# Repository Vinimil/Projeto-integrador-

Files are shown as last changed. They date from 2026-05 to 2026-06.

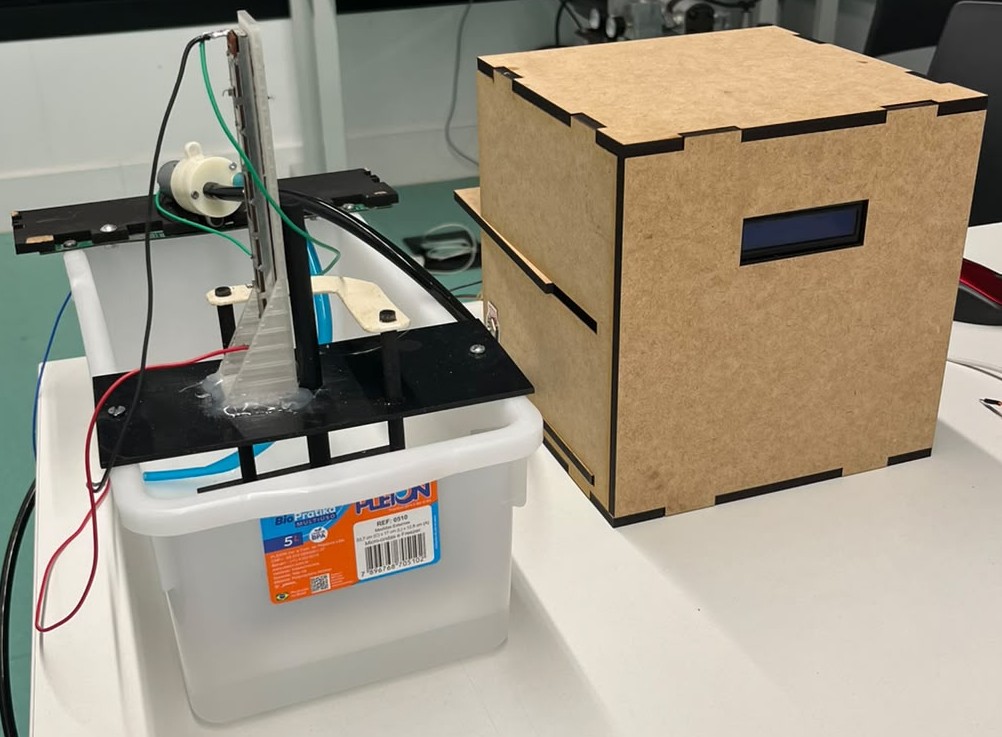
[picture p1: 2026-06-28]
Imagem projeto2.jpg

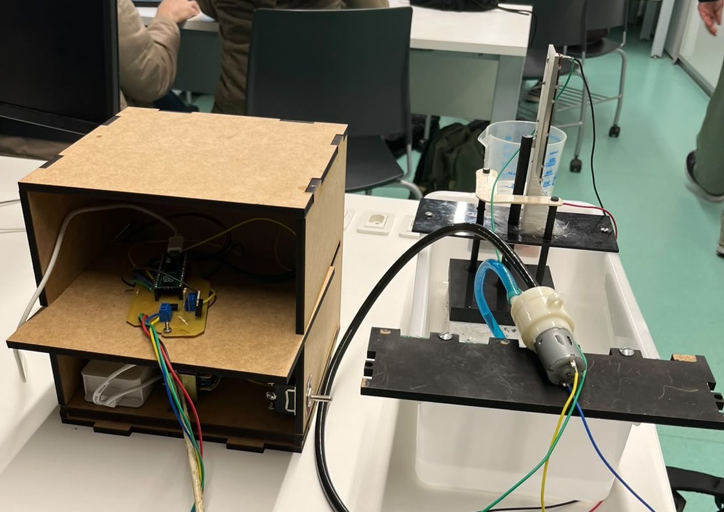
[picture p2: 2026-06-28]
Imagem projeto1.jpg

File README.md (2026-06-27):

Sistema de Dosagem Automática de Água com Raspberry Pi Pico

1.Integrantes:

João Lourenço Medeiros Martins (RA: 22.00369-0)
Nicolas Lemos Nunes Tamashiro (RA: 22.00728-8)
Theo Franchin Peres (RA: 22.01094-7)
Vinicius Filgueiras dos Santos (RA: 23.95007-2)

2.Descrição do projeto:

Este projeto propõe um sistema embarcado de automação para controle de nível e dosagem volumétrica de fluidos entre reservatórios (TK-101 e TK-102), utilizando um Raspberry Pi Pico (RP2040) como unidade central de processamento. A automação integra um transdutor de nível resistivo (potenciômetro linear) condicionado por filtros digitais FIR, IHM em display LCD I2C e acionamento de potência via optoacoplamento e MOSFET, garantindo isolamento galvânico e controle preciso de vazão por modulação de pulsos.

3.Objetivos:

-Realizar dosagem precisa retirando líquido de um reservatório principal.
-Converter a posição do sensor em volume real (mL).
-Permitir a seleção de dosagens pré-definidas.
-Controlar automaticamente a bomba hidráulica.
-Interromper a dosagem ao atingir o volume desejado.
-Exibir informações do processo em um display LCD.
-Implementar estratégia de controle em malha fechada via realimentação.

4.Arquitetura do Sistema:

4.1 Composição:
-Reservatório 1: Principal (medição e retirada).
-Reservatório 2: Receptor.
-Sensor de Nível: Potenciômetro linear acoplado a flutuador.
-Raspberry Pi Pico: Responsável por aquisição de sinais, conversão ADC, processamento, controle da bomba e interface LCD.
-Módulo MOSFET: Acionamento da bomba.
-Display LCD 16x2 I2C: Interface visual.

4.2 Funcionamento Geral:
-Leitura do sensor de nível.
-Conversão ADC (12 bits) para valor digital.
-Conversão do valor ADC para volume (mL) via tabela de calibração.
-Seleção de dosagem pelo usuário.
-Cálculo do erro de dosagem em tempo real e acionamento da bomba via malha fechada com realimentação contínua, utilizando zonas de tempo (1200ms, 700ms e 300ms) para amortecimento da inércia mecânica.
-Leitura, verificação do volume transferido e correção, repetindo o ciclo até atingir a meta.

5.Hardware:

Componente             Conexão

Potenciômetro          Terminal 1: 3V3 / Cursor: GP26 (ADC0) / Terminal 2: GND
Display LCD	           VCC: 5V / GND: GND / SDA: GP8 / SCL: GP9
MOSFET	Gate           GP15
Terminal 1	           3V3
Cursor	               GP26 (ADC0)
Terminal 2	           GND
A bomba  é alimentada externamente 

Display:

LCD 16x2
Interface I2C
Endereço: 0x27

5.1 Características:

Alimentação: 3,3 V
Saída analógica
Ligado diretamente ao ADC do Pico

6.Estratégia de Medição e Calibração:

-Conversão ADC: Escala de 0 a 4095.
-Filtragem: Média de 500 amostras consecutivas seguida por um filtro de 20 leituras úteis.
-Calibração: Utilização de tabela experimental com interpolação linear para valores intermediários.
-Pontos de calibração: 
ADC	Volume (mL)
3057	0
3054	200
3041	400
529	3000

7.Estratégia de Controle

-Malha Fechada: Realimentação baseada no volume calculado.
-Controle por Pulsos:
-Região Longa: Pulsos de 1200 ms (alta velocidade).
-Região Intermediária: Pulsos de 700 ms (redução de velocidade).
-Região Final: Pulsos de 300 ms (ajuste fino para precisão).
-Correção de Volume:
-Fator de 1.22 para dosagens de 250 mL.
-Fator de 1.44 para dosagens de 300 mL e 350 mL.

8.Interface LCD e Resultados:

Status de Operação: Tela inicial, Dosagem em execução e Processo finalizado.
Resultados Observados: O sistema apresentou repetibilidade satisfatória, com resultados médios de ≈ 250 mL, ≈ 300 mL e ≈ 350 mL para as respectivas doses solicitadas.

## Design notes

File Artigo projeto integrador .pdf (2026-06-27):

SISTEMA EMBARCADO PARA CONTROLE E MEDIÇÃO VOLUMÉTRICA DE

RESERVATÓRIOS: UMA ABORDAGEM DE BAIXO CUSTO UTILIZANDO O

MICROCONTROLADOR RP2040

João Lourenço Medeiros Martins¹; Nicolas Lemos Nunes Tamashiro¹; Theo Franchin

Peres¹; Vinicius Filgueiras dos Santos¹; Andressa Corrente Martins²; Rodrigo de Marca

França²

¹ Docente do Instituto Mauá de Tecnologia (IMT)

² Docente do Instituto Mauá de Tecnologia (IMT)

Resumo

Este artigo apresenta o desenvolvimento, a implementação e a validação

experimental de um sistema embarcado de automação concebido para o

monitoramento contínuo e o controle em malha fechada da transferência volumétrica de

fluidos entre reservatórios. A arquitetura de hardware baseia-se no microcontrolador

RP2040, explorando seu conversor analógico-digital de 12 bits para a aquisição de

dados provenientes de um transdutor de nível resistivo, construído por meio do

acoplamento mecânico de um potenciômetro linear a um flutuador fixado em uma

estrutura manufaturada em PLA. Com o intuito de mitigar as perturbações

hidrodinâmicas e outras interferências, o sinal analógico foi condicionado por um filtro

passa-baixas passivo e processado por um filtro digital FIR de médias móveis. A

estratégia de controle atua por realimentação contínua, compensando os efeitos da

inércia do atuador (bomba de diafragma de corrente contínua) por meio de um

algoritmo de comutação dividido em três faixas de erro. A calibração da leitura foi

realizada mediante interpolação linear por partes e a aplicação de fatores corretivos

(1,22 e 1,44). Os ensaios comprovaram a resiliência da malha, registrando erro relativo

máximo de -2,40% e erro relativo nulo dentro da resolução experimental para a meta de

300 mL. O protótipo atesta a viabilidade do emprego de instrumentação alternativa para

processos de pequena escala.

Palavras-chave: RP2040. Realimentação Contínua. Instrumentação Eletrônica.

Automação. Filtro Digital.

### 1 INTRODUÇÃO

### 1 INTRODUÇÃO

No contexto da automação de processos industriais e laboratoriais, a exatidão no

controle e na dosagem contínua de fluidos é um requisito importante para garantir a

qualidade e a repetibilidade operacional (Bolton, 2015). A expansão dos sistemas

embarcados voltados à automação tem impulsionado o desenvolvimento de soluções

de baixo custo e alta confiabilidade, oferecendo uma alternativa técnica e

economicamente viável aos sensores industriais tradicionais (Dorf; Bishop, 2011).

Este trabalho apresenta o desenvolvimento, a implementação e a validação

experimental de um sistema automatizado para monitoramento e controle volumétrico

da transferência de água entre dois reservatórios. A planta didática, projetada conforme

a norma ISA 5.1 (ISA, 2024), é composta pelos tanques TK-101 e TK-102, interligados

hidraulicamente, sendo a variável controlada o volume de água transferido entre eles.

O processamento dos sinais do transdutor de nível e o acionamento dos

elementos finais de controle são realizados pelo microcontrolador RP2040 (Raspberry

Pi Foundation, 2024). O sistema realiza a conversão analógico-digital das leituras do

sensor, executa uma malha fechada de controle e disponibiliza as informações ao

operador por meio de uma Interface Homem-Máquina (IHM) baseada em display LCD

16×2 com comunicação I2C, além da transmissão de dados via porta serial (UART).

Devido à inércia da bomba de diafragma, à latência do escoamento e às

limitações de resolução do sensor, foi desenvolvida uma estratégia de controle baseada

em filtragem digital, calibração empírica e acionamento do atuador por comutação em

faixas de erro, visando aumentar a precisão da dosagem e a estabilidade do sistema.

### 2 MATERIAIS E MÉTODOS

A metodologia adotada foi dividida em três etapas interrelacionadas: o

desenvolvimento do arranjo mecânico, a implementação do hardware eletrônico de

condicionamento, e a implementação da malha de realimentação no firmware.

### 2.1 Estrutura Mecânica e Transdutor Analógico

A aferição contínua do nível baseia-se em um transdutor resistivo baseado em

um potenciômetro linear acoplado. O cursor metálico de um potenciômetro deslizante

foi fixado mecanicamente a uma haste sólida tracionada por um flutuador no

reservatório TK-101. Para assegurar a ortogonalidade do movimento e prevenir o

travamento provocado por esforços laterais, desenvolveu-se uma estrutura de suporte

mecânico rígida. O esquemático de interligação dos reservatórios e do sistema de

bombeamento pode ser visualizado na Figura 1, detalhando a topologia adotada.

Figura 1 - Esquemático do sistema detalhando a interligação entre os tanques e a

bomba.

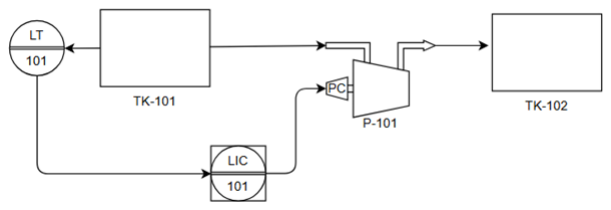
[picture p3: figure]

Fonte: Elaborado pelos autores (2026).

As peças e as fixações do potenciômetro foram modeladas em ambiente CAD

tridimensional utilizando o software SolidWorks e manufaturadas em uma impressora

3D com polímero ácido polilático (PLA), conforme ilustra a Figura 2, que evidencia o

arranjo físico projetado para a haste.

Figura 2 - Modelagem em CAD (SolidWorks) das fixações estruturais do transdutor.

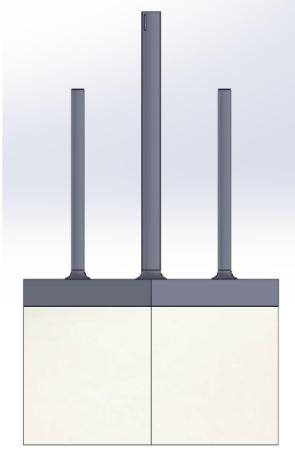
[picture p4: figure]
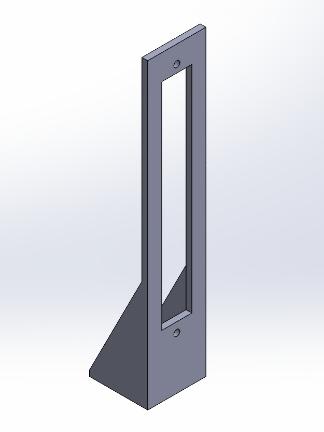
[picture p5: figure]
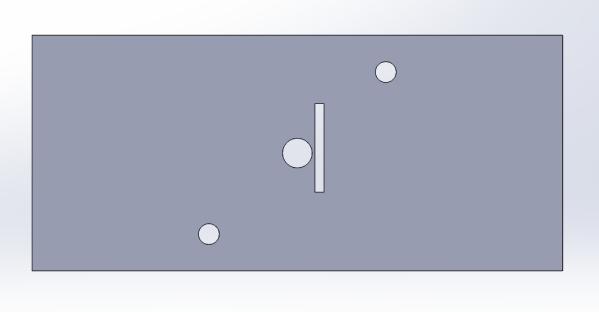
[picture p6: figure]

Fonte: Elaborado pelos autores (2026).

O divisor de tensão resultante no cursor do potenciômetro é polarizado por uma

tensão de referência restrita de 3,3 V, de modo que o deslocamento físico da boia

acompanhando o nível do fluido se traduz proporcionalmente em variação de potencial

elétrico encaminhada ao canal de conversão (ADC) do microcontrolador.

### 2.2 Microcontrolador e Condicionamento de Sinais

O processamento centraliza-se no microcontrolador RP2040. A fim de atenuar os

ruídos e as interferências acopladas aos condutores do sensor resistivo, foi projetado

um filtro analógico passa-baixas passivo composto por uma rede resistor-capacitor

(RC).

Adotando-se um componente resistivo de 10 kΩ e uma capacitância de 100 nF, a

frequência de corte (fc) teórica, segundo as premissas de Sedra e Smith (2014), é

calculada pela Equação 1:

fc =

1
2π. R. C

=

1
2π. 10. 10³. 100. 10⁻⁹ = 159,15 Hz

Este limiar de aproximadamente 159 Hz reduz os fenômenos de aliasing elétrico

de alta frequência, mantendo as componentes de baixa frequência originadas da

movimentação mecânica.

### 2.3 Circuito de Potência e Isolamento Galvânico

Devido às limitações de capacidade de corrente das portas GPIO do microcontrolador e

à imperatividade de proteção contra transientes indutivos, foi implementado um estágio

de acionamento baseado em comutação por estado sólido.

A interface entre o subsistema de controle (3,3V) e o estágio de potência (7,5V) é

realizada mediante isolamento galvânico via optoacoplador PC817. Esta topologia

assegura a segregação elétrica completa, mitigando o acoplamento de ruídos e

transientes de tensão induzidos pela carga indutiva das bombas ao microcontrolador.

Em conformidade com as diretrizes de integridade de sinal, a topologia da PCB contempla a separação estrita entre os planos de terra (GND) dos domínios de controle

e de potência.

O sinal de controle, após atravessar o isolador, é aplicado ao terminal de gate de um

transistor MOSFET, configurado para operar como chave de estado sólido. A transição

para nível lógico alto satura o optoacoplador, polarizando o gate e conduzindo o

MOSFET à região de condução, permitindo o acionamento da carga via Low-Side

Switching. Esta configuração possibilita a comutação eficiente de cargas de 10A,

garantindo estabilidade térmica e a integridade da lógica de controle. Adicionalmente, a

robustez operacional do sistema é assegurada pela utilização de fontes de alimentação

independentes: um barramento de 5V dedicado à unidade de processamento (RP2040)

e display, e um barramento isolado de 7,5V exclusivo para o estágio de potência das

bombas permitindo a topologia de isolamento.

Figura 3 – Diagrama Elétrico

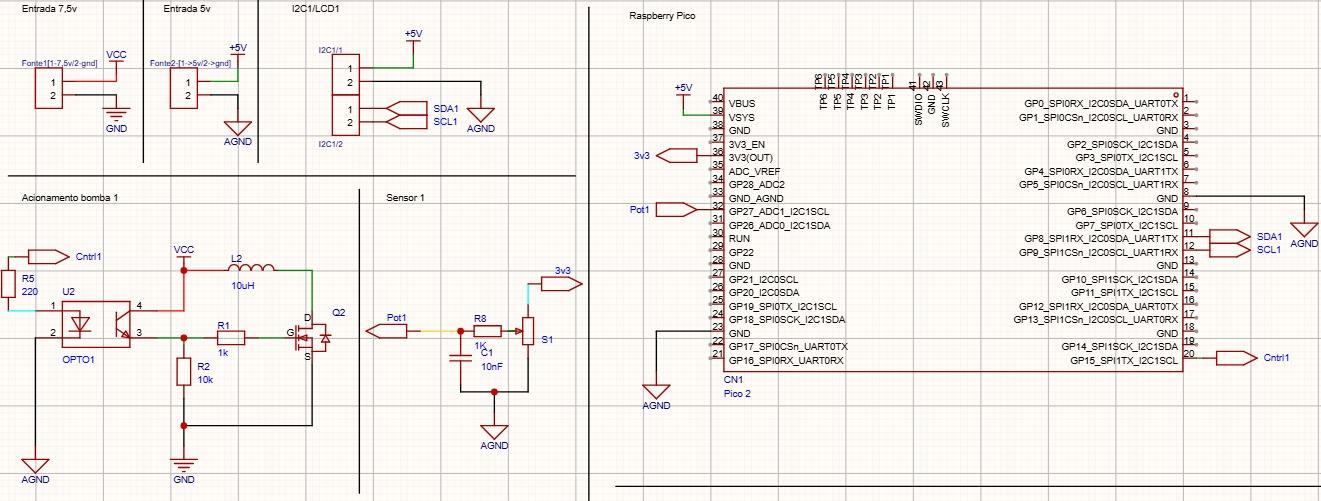
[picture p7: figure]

Fonte: Elaborado pelos autores (2026).

### 2.4 Modelagem Algorítmica e Filtragem Digital

O sinal digitalizado no ADC (0 a 4095) encontra-se sujeito a oscilações da

superfície do líquido durante o impacto do recálque. Implementou-se no firmware um

filtro digital Finite Impulse Response (FIR) por médias móveis. O algoritmo consolida a captura contínua de 500 amostras analógicas consecutivas por ciclo. Em seguida, essa

saída alimenta uma segunda janela de filtragem restrita que retém as últimas 20

leituras, garantindo a atenuação significativa dos ruídos transientes.

Devido ao atrito mecânico, o sistema apresenta falhas de linearidade nas pontas

da escala. Parametrizou-se em software uma tabela relacionando pontos específicos de

leitura a volumes hídricos reais (calibração). Para estimar em tempo real os volumes

situados entre os pontos de calibração, o sistema executa uma interpolação linear

paramétrica segmentada, descrita pela Equação 2:

V = V1 + [

ADC − ADC1
ADC2 − ADC1

]. (V2 − V1)

Onde V é o volume de fluido estimado em tempo real; ADC é a leitura

instantânea filtrada do conversor; ADC1 e ADC2 são os limites tabelados vizinhos à

leitura; e V1 e V2 denotam os volumes absolutos correspondentes a esses limites.

### 2.5 Estratégia de Controle e Realimentação Contínua

A topologia adotada atua através de uma malha fechada direta de realimentação

contínua. O diagrama de blocos apresentado na Figura 4 apresenta essa arquitetura: o

sinal captado pelo sensor de nível é injetado em um nó comparador interno no RP2040,

gerando continuamente o sinal de erro em relação à meta arbitrada. Com base neste

erro, o microcontrolador processa a resposta e atua sobre a bomba de diafragma, cujo

fluxo físico altera o nível do reservatório e realimenta o laço do sensor.

Figura 4 - Diagrama de blocos do sistema, evidenciando o laço de realimentação

contínua de estado.

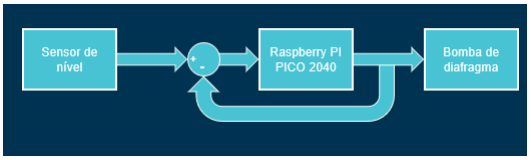
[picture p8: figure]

Fonte: Elaborado pelos autores (2026).

Para reduzir o escoamento residual da tubulação (fluido remanescente em

escoamento após a remoção da alimentação elétrica), o atuador não opera de maneira

simples (Liga/Desliga direto), sendo modulado em três zonas de tempo baseadas na

amplitude instantânea do erro:

- Região de Erro Elevado (Erro > 180 mL): Acionamento da bomba em janelas

largas de 1200 ms.

- Região de Erro Intermediário (50 mL < Erro ≤ 180 mL): Redução do tempo de

pulso para 700 ms, induzindo gradiente de desaceleração.

- Região de Erro Crítico (Erro ≤ 50 mL): Saturação ativa com pulsos de 300 ms,

para correção de ajuste fino.

Inseriu-se um tempo morto (dead time) compulsório de 300 ms após cada ciclo

de pulso, permitindo que a ondulação do fluido se estabilize antes de uma nova leitura

ser consolidada no comparador. O ganho estático foi parametrizado em 1,22 para

dosagens de 250 mL e 1,44 para as metas superiores.

O comissionamento e o monitoramento operacional são estabelecidos por meio

de um módulo de cristal líquido (LCD 16x2) com expansor I2C. A interface foi

programada para fornecer ao operador um feedback visual dinâmico em tempo real: a

primeira linha do display apresenta a variável analógica bruta processada pelo ADC,

denominada T (referente à tensão normalizada do potenciômetro), enquanto a segunda

linha exibe o Volume atual calculado após a aplicação das rotinas de filtragem FIR e da

interpolação linear parametrizada. Essa estrutura de exibição garante a supervisão

direta da conversão eletroeletrônica do sinal, permitindo a validação visual imediata da

calibração do sensor.

### 3 RESULTADOS E DISCUSSÃO

A certificação da integridade da planta experimental baseou-se na execução de

ensaios repetitivos e parametrizados. Extraiu-se um conjunto de ensaios onde os

volumes transferidos ao TK-102 foram quantificados mediante um copo graduado,

validando a eficácia e a repetibilidade da lógica proposta visando as metas volumétricas

de 250 mL, 300 mL e 350 mL.

A Tabela 1 expõe a consolidação da capacidade corretiva dos fatores

matemáticos adotados na modelagem, refletindo o desvio numérico após a aplicação

do laço de realimentação.

Tabela 1 - Desempenho metrológico e erro relativo das dosagens automatizadas.

Meta definida (mL) | Leitura Bruta do Sensor (mL) | Volume Estimado Corrigido (mL) | Aferição Real Medida (mL) | Erro Relativo (%)
250 | 173 | 249 | 244 | -2,40
300 | 209 | 301 | 300 | 0,00
350 | 243 | 350 | 348 | -0,57

Fonte: Elaborado pelos autores (2026).

A análise sistemática aponta para um desempenho satisfatório. Nas

aproximações nominais de 300 mL e 350 mL, as margens relativas demonstraram alta

concordância (registrando 0,00% e -0,57%, respectivamente). Na região de dosagem

reduzida (250 mL), o erro relativo permaneceu no teto administrável de -2,40%.

Ensaios preliminares sem a modulação por zonas resultavam em sobre-dosagem

maciça (overshoot) variando entre 15% e 20% acima do setpoint. O motor continuava

rotacionando devido ao momentum da bomba de diafragma, e a coluna residual

pendente drenava gravitacionalmente. A fragmentação do esforço de controle nas

janelas de 1200, 700 e 300 milissegundos reduziu essa extrapolação.

Para elucidar a eficácia da regressão linear, os gráficos a seguir ilustram as

curvas de calibração empírica relacionando o volume real retirado com a estimativa

processada. Observa-se a correção da histerese e a convergência após a aplicação

dos fatores multiplicativos correspondentes (1,22 e 1,44).

Gráfico 1 - Curva de calibração comparativa para a meta de 250 mL (Fator 1,22).

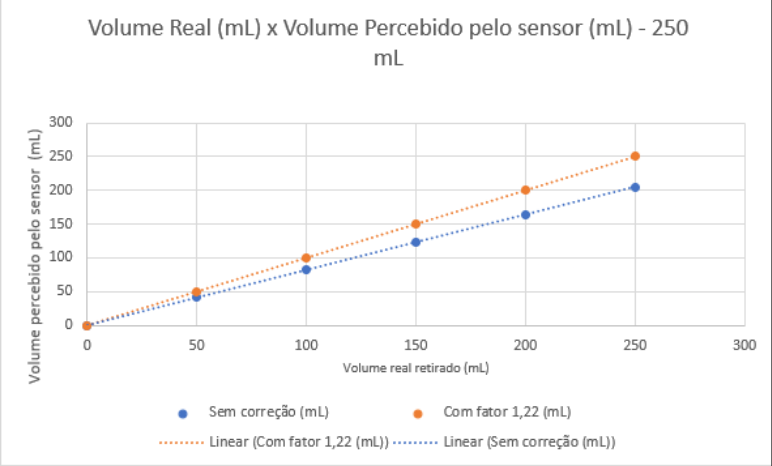
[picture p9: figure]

Fonte: Elaborado pelos autores (2026).

Gráfico 2 - Curva de calibração comparativa para a meta de 300 mL (Fator 1,44).

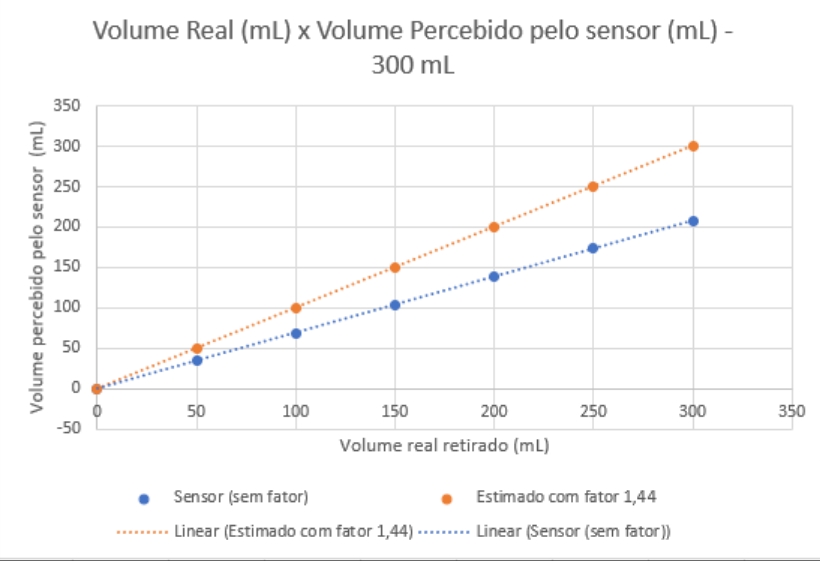
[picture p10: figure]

Fonte: Elaborado pelos autores (2026).

### 4 CONCLUSÕES

O projeto alcançou o objetivo de automatizar a medição e a dosagem contínua

de fluidos com elevada precisão, utilizando uma arquitetura de realimentação em malha

fechada baseada no microcontrolador RP2040, sem recorrer a algoritmos adaptativos

complexos. O sistema foi capaz de executar as rotinas de filtragem digital, gerenciar a

planta e controlar a interface I2C de forma integrada.

As limitações construtivas do transdutor resistivo, decorrentes do contato

mecânico entre o potenciômetro e o sistema de flutuação, foram compensadas pela aplicação de interpolação linear segmentada e fatores de calibração associados às

faixas de operação do controle.

Como principal limitação para aplicações industriais, destaca-se o desgaste da

trilha resistiva do potenciômetro. Assim, recomenda-se, em trabalhos futuros, a

substituição do sensor por tecnologias sem contato, como sensores capacitivos, bem

como a investigação de estratégias de controle lineares, visando ampliar a flexibilidade

para diferentes setpoints e aplicações em maior escala.

REFERÊNCIAS

Bolton, W. Instrumentação e controle. 6. ed. São Paulo: Hemus, 2015.

Dorf, R. C.; Bishop, R. H. Modern control systems. 12. ed. New Jersey: Pearson, 2011.

ISA - International Society of Automation. ANSI/ISA-5.1-2024: instrumentation and

control - symbols and identification. Research Triangle Park, NC: ISA, 2024.

SANTOS, Vinicius Filgueiras dos. Projeto Integrador: Sistema de Dosagem Automática de Água. GitHub, 2026. Disponível em: https://github.com/Vinimil/Projeto-integrador-.

Acesso em: 22 jun. 2026

.Raspberry Pi Foundation. Raspberry Pico datasheet. Cambridge, 2024. Disponível em:

https://datasheets.raspberrypi.com/pico/pico-datasheet.pdf. Acesso em: 1 jun. 2026.

Sedra, A. S.; Smith, K. C. Microeletrônica. 6. ed. São Paulo: Makron Books, 2014.

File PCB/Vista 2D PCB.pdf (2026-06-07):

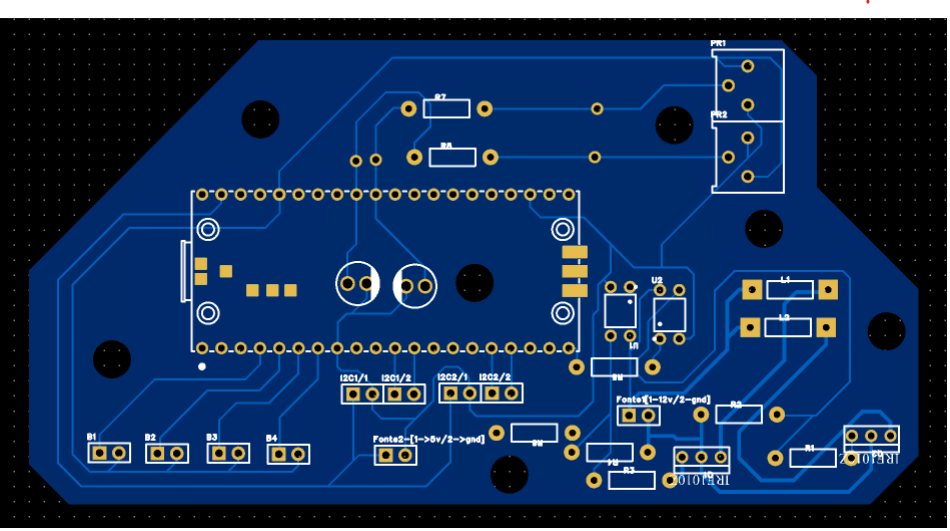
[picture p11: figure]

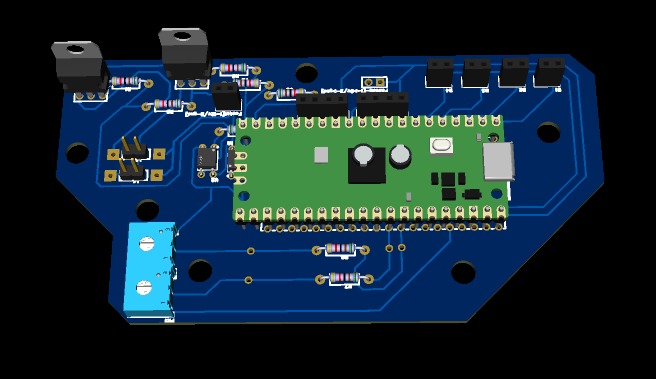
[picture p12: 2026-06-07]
PCB/Vista 3D PCB.jpeg

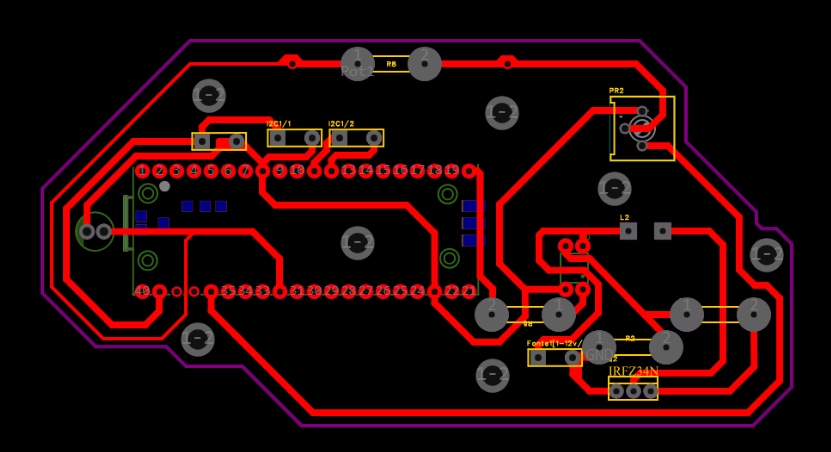
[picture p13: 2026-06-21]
PCB/imagem_2026-06-21_175348476.png

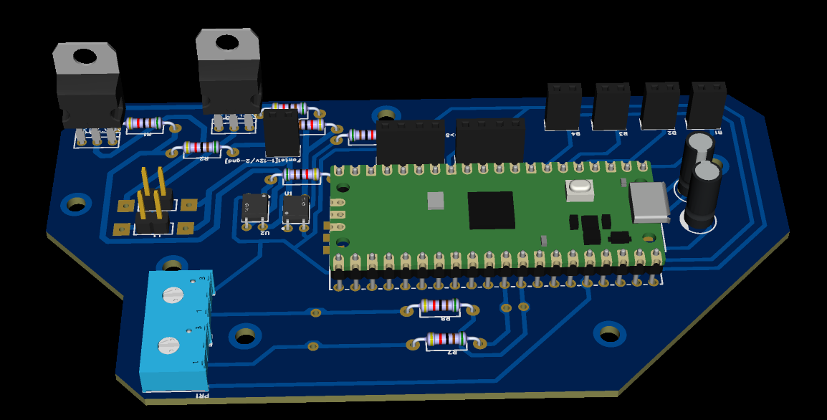
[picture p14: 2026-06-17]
PCB/imagem_2026-06-16_222955062.png

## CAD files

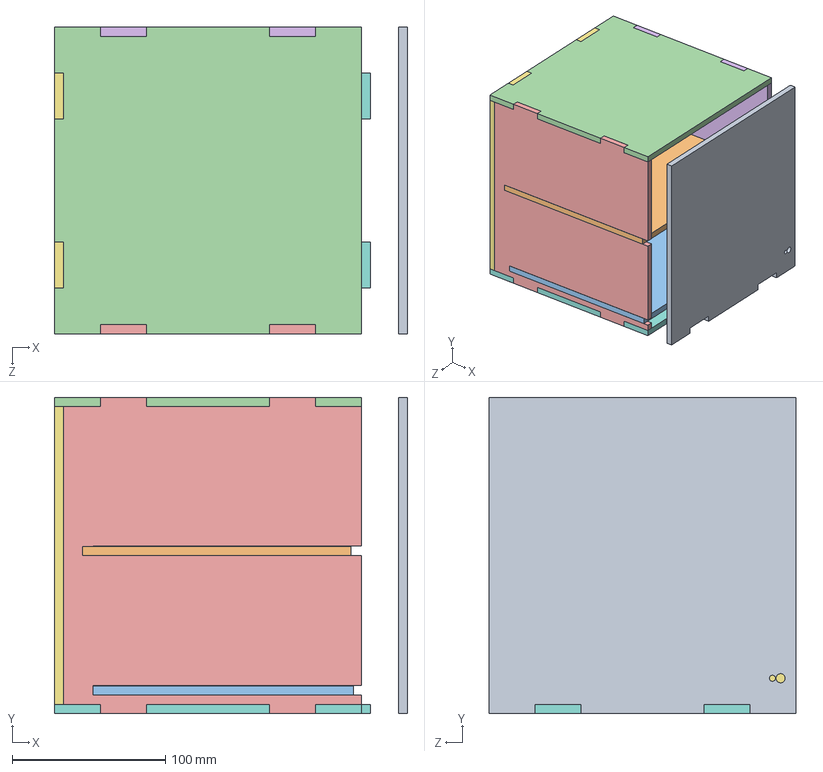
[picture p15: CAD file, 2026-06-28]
solidworks/Suporte Eletronica/Montagem.SLDASM
230.0 x 206.0 x 200.0 mm
chão
frente
lado 1
lado 2
teto
prateleira 1
prateleira 2
tampa traseira

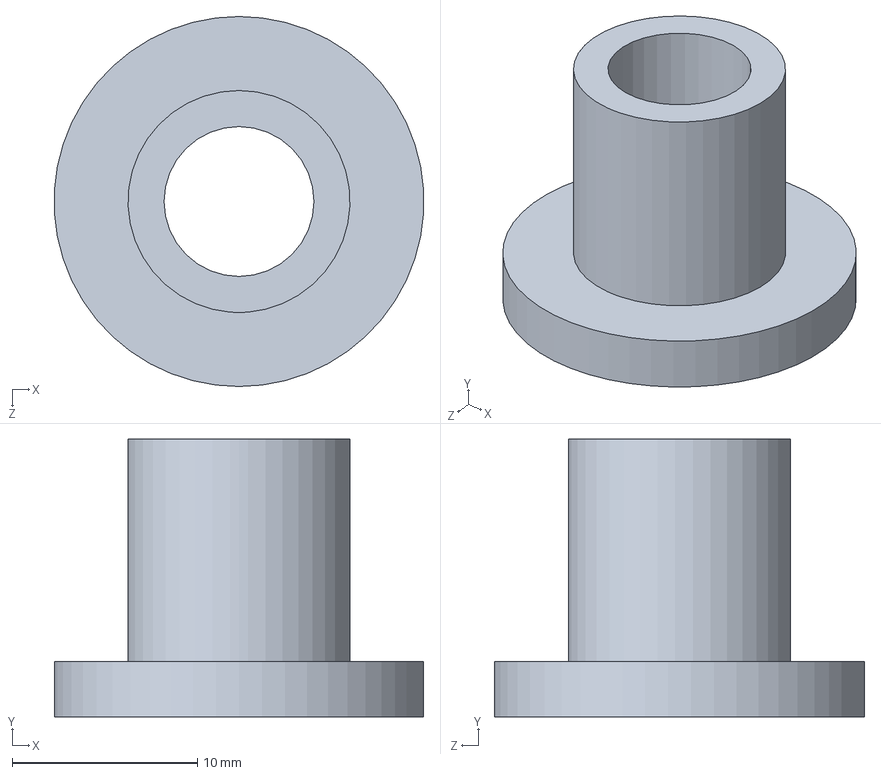
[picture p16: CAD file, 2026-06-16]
solidworks/bucha 8.SLDPRT
20.0 x 15.0 x 20.0 mm

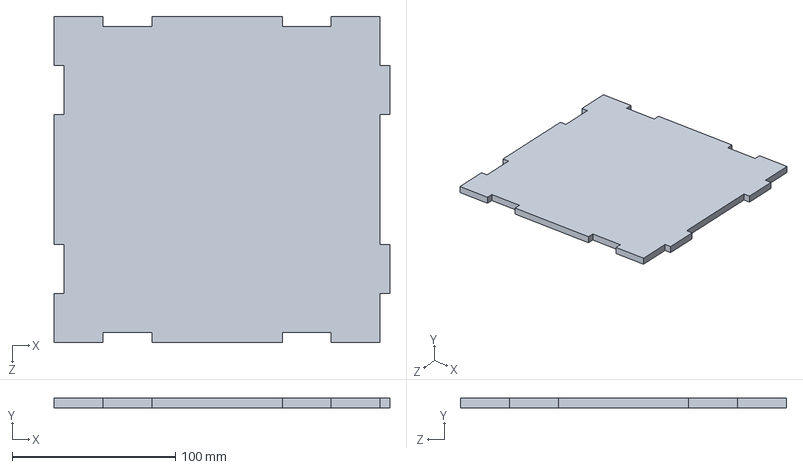
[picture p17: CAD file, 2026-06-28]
solidworks/Suporte Eletronica/chão.SLDPRT
206.0 x 6.00 x 200.0 mm

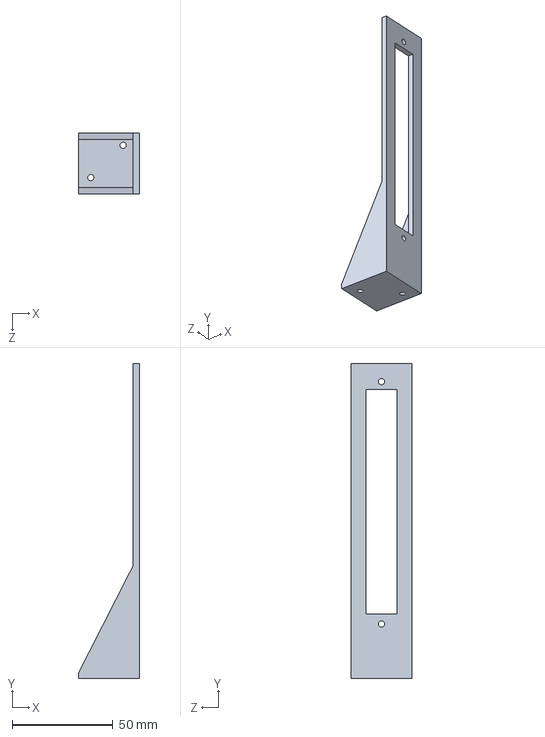
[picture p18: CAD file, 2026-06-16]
solidworks/base.SLDPRT
30.0 x 156.0 x 30.0 mm

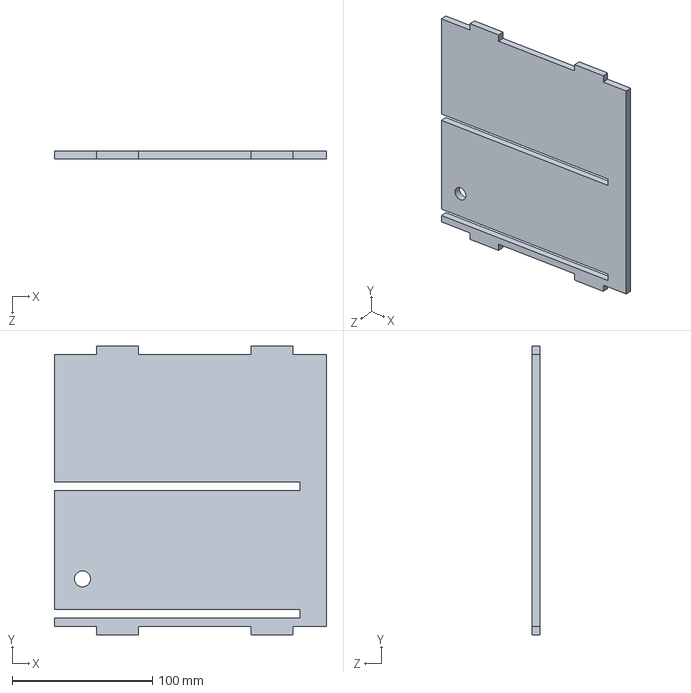
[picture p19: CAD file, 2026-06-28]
solidworks/Suporte Eletronica/lado 1.SLDPRT
194.0 x 206.0 x 6.00 mm

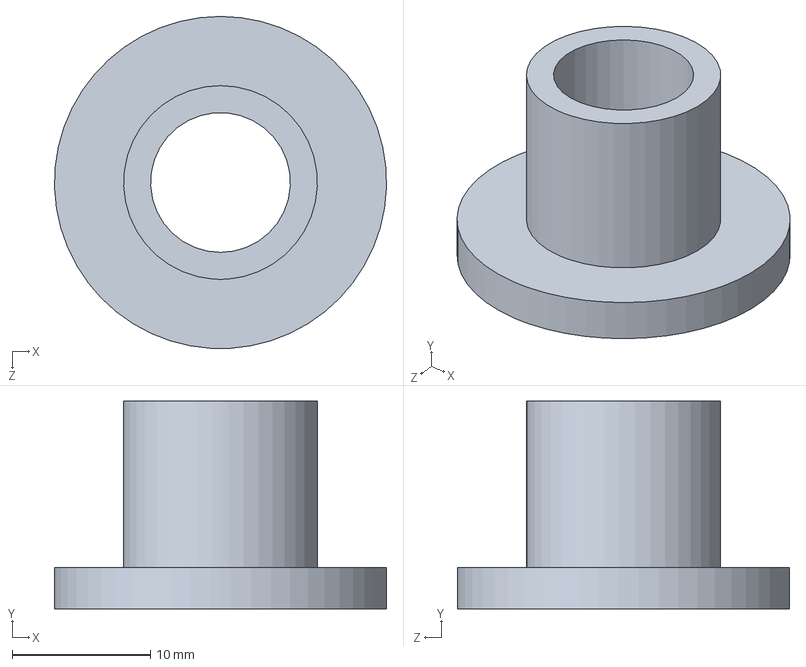
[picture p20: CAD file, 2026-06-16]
solidworks/bucha 10.SLDPRT
24.0 x 15.0 x 24.0 mm

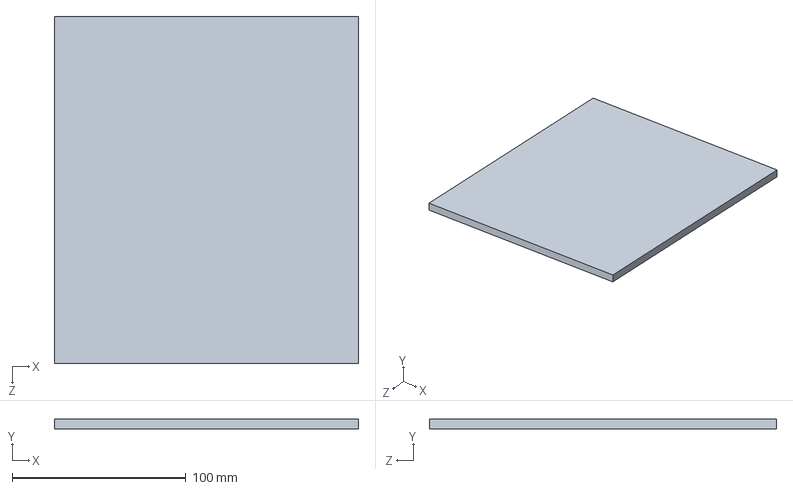
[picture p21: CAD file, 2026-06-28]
solidworks/Suporte Eletronica/prateleira 2.SLDPRT
175.0 x 6.00 x 200.0 mm

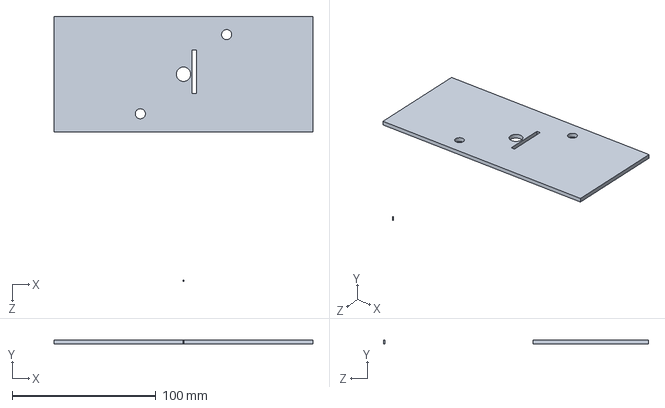
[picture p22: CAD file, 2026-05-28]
solidworks/tampa v3.SLDPRT
180.0 x 3.00 x 183.9 mm

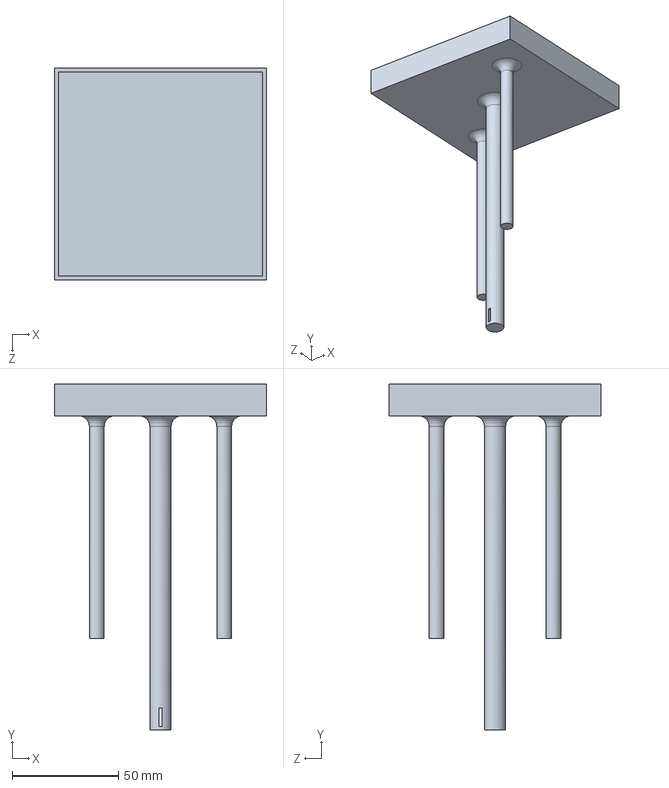
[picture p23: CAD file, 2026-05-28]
solidworks/boia.SLDPRT
100.0 x 163.0 x 100.0 mm

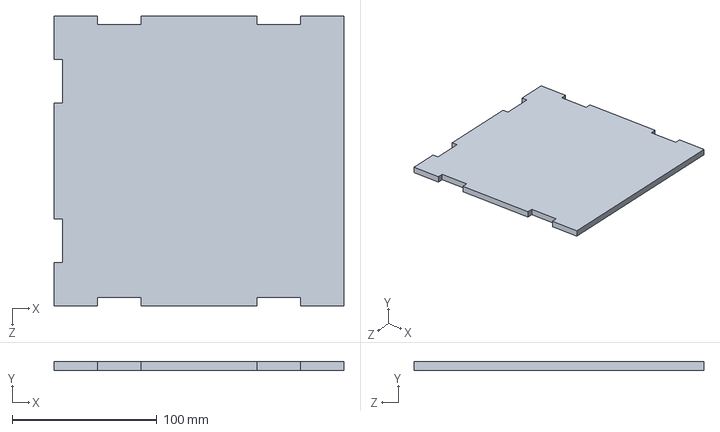
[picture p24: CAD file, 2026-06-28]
solidworks/Suporte Eletronica/teto.SLDPRT
200.0 x 6.00 x 200.0 mm

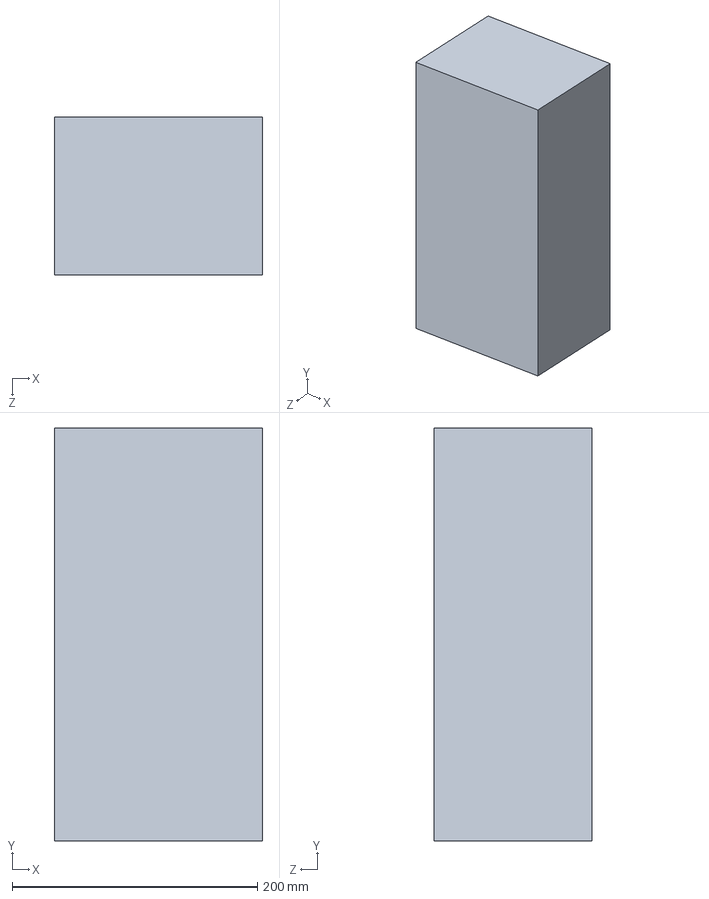
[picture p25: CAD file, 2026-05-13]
solidworks/pote 5l simulação.SLDPRT
170.0 x 337.0 x 129.0 mm

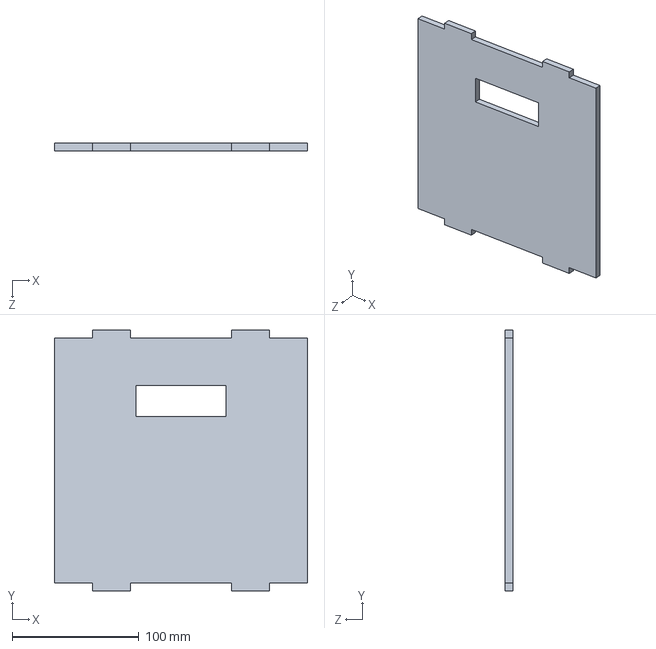
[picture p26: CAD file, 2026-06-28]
solidworks/Suporte Eletronica/frente.SLDPRT
200.0 x 206.0 x 6.00 mm

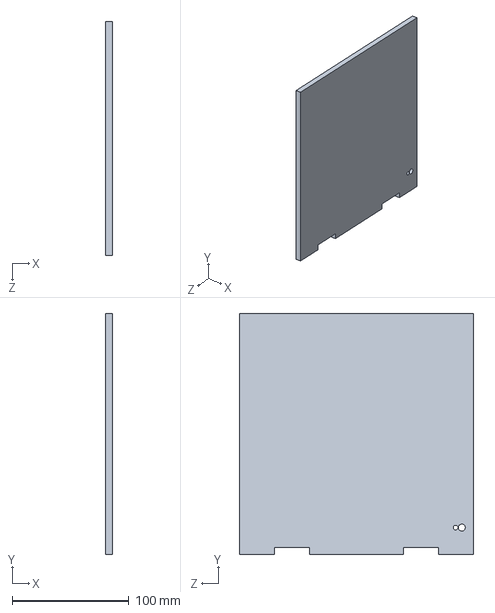
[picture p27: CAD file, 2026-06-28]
solidworks/Suporte Eletronica/tampa traseira.SLDPRT
6.00 x 206.0 x 200.0 mm

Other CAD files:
solidworks/Suporte Eletronica/lado 2.SLDPRT

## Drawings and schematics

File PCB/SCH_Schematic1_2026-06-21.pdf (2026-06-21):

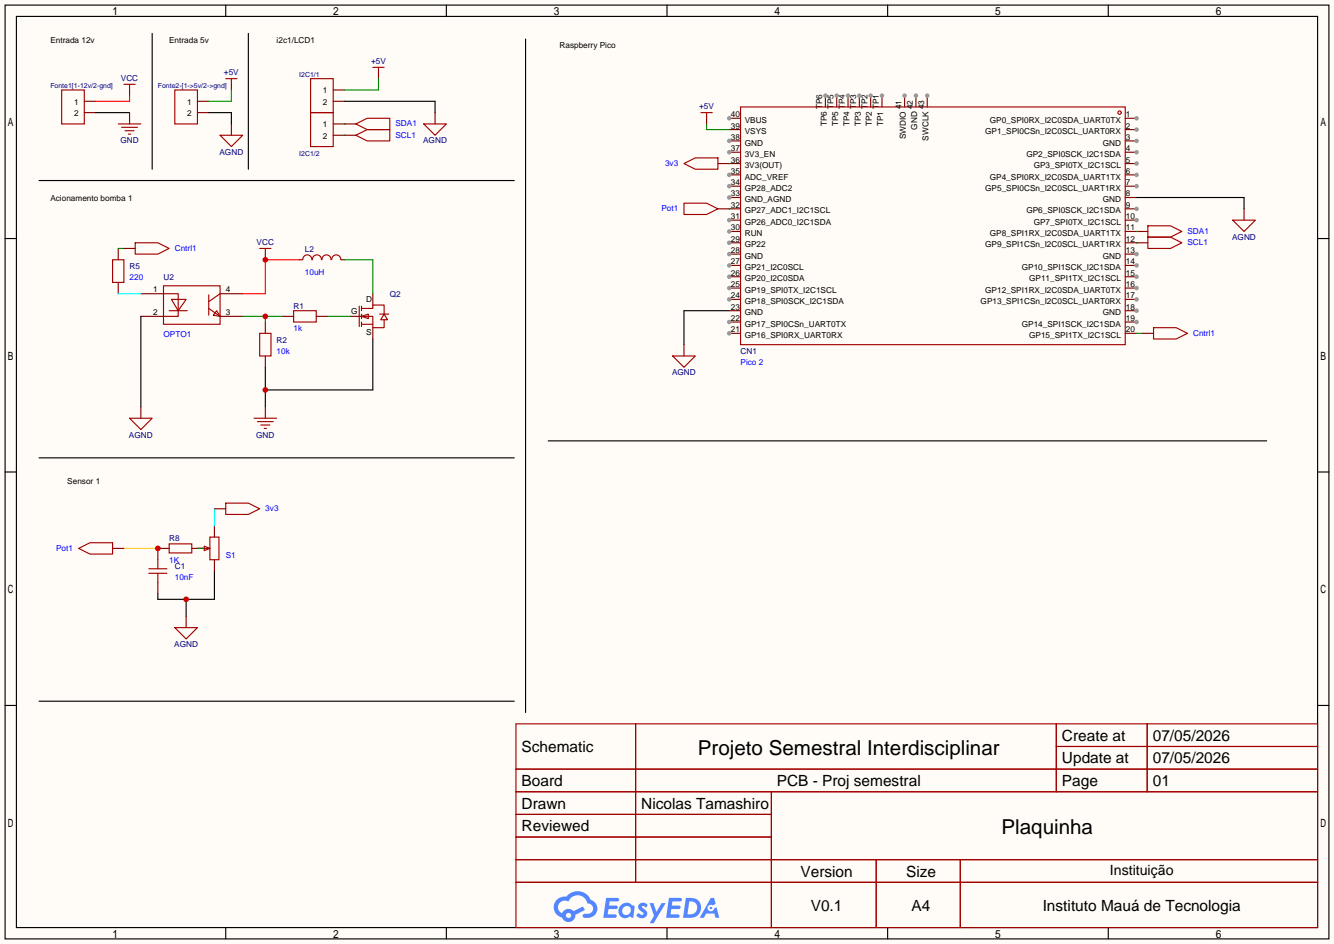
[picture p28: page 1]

Schematic | Projeto Semestral Interdisciplinar | Create at | 07/05/2026

Update at | 07/05/2026

Board | PCB - Proj semestral | Page | 01
Drawn | Nicolas Tamashiro | Plaquinha
Reviewed

Version | Size | Instituição
V0.1 | A4 | Instituto Mauá de Tecnologia

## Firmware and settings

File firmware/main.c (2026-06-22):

#include <stdio.h>
#include <stdlib.h>
#include <math.h>

#include "pico/stdlib.h"
#include "pico/stdio_usb.h"
#include "hardware/gpio.h"

#include "config.h"
#include "adc.h"
#include "calibracao.h"
#include "lcd_i2c.h"

float obter_fator(float dose_ml)
{
    if(dose_ml <= 250)
        return 1.22f;

    return 1.44f;
}

float adc_para_tensao(uint16_t adc)
{
    return (adc * 3.3f) / 4095.0f;
}

void bomba_setup(void)
{
    gpio_init(BOMBA_PIN);
    gpio_set_dir(BOMBA_PIN, GPIO_OUT);
    gpio_put(BOMBA_PIN, 0);
}

void bomba_ligar(void)
{
    gpio_put(BOMBA_PIN, 1);
}

void bomba_desligar(void)
{
    gpio_put(BOMBA_PIN, 0);
}

float ler_volume_filtrado(void)
{
    float soma = 0;

    for(int i = 0; i < FILTRO_LEITURAS; i++)
    {
        soma += adc_para_volume(adc_read_raw());
        sleep_ms(5);
    }

    return soma / FILTRO_LEITURAS;
}

void aplicar_pulso(uint32_t tempo_ms)
{
    bomba_ligar();
    sleep_ms(tempo_ms);
    bomba_desligar();
}

void mostrar_tela_principal(void)
{
    uint16_t adc = adc_read_raw();

    float tensao =
        adc_para_tensao(adc);

    float volume =
        ler_volume_filtrado();

    char linha1[17];
    char linha2[17];

    snprintf(linha1,
             sizeof(linha1),
             "Vol:%4.0fmL",
             volume);

    snprintf(linha2,
             sizeof(linha2),
             "T:%1.2fV",
             tensao);

    lcd_clear();

    lcd_set_cursor(0,0);
    lcd_print(linha1);

    lcd_set_cursor(0,1);
    lcd_print(linha2);
}

void modo_calibracao(void)
{
    char entrada[32];

    printf("\n");
    printf("====================================\n");
    printf("MODO CALIBRACAO\n");
    printf("====================================\n");
    printf("Digite -1 para sair\n\n");

    while(true)
    {
        uint16_t adc =
            adc_read_raw();

        float tensao =
            adc_para_tensao(adc);

        float volume_atual =
            adc_para_volume(adc);

        lcd_clear();

        char linha1[17];
        char linha2[17];

        snprintf(linha1,
                 sizeof(linha1),
                 "T:%1.2fV",
                 tensao);

        snprintf(linha2,
                 sizeof(linha2),
                 "Vol:%4.0fmL",
                 volume_atual);

        lcd_set_cursor(0,0);
        lcd_print(linha1);

        lcd_set_cursor(0,1);
        lcd_print(linha2);

        printf("\n");
        printf("------------------------------------\n");
        printf("ADC    : %u\n", adc);
        printf("Tensao : %.3f V\n", tensao);
        printf("------------------------------------\n");
        printf("Volume (mL): ");

        scanf("%31s", entrada);

        float volume =
            atof(entrada);

        if(volume < 0)
        {
            printf("\nSaindo da calibracao...\n");
            break;
        }

        adc = adc_read_raw();

        printf("\n");
        printf("ADC = %u -> %.0f mL\n",
               adc,
               volume);

        printf("Tabela para copiar:\n");
        printf("%u,\n", adc);
    }
}

void dosar(float dose_ml)
{
    float fator =
        obter_fator(dose_ml);

    uint16_t adc_inicial =
        adc_read_raw();

    float volume_inicial =
        ler_volume_filtrado();

    printf("\n====================================\n");
    printf("INICIANDO DOSAGEM\n");
    printf("====================================\n");
    printf("Tensao inicial : %.2f V\n",
           adc_para_tensao(adc_inicial));
    printf("Volume inicial : %.0f mL\n",
           volume_inicial);
    printf("Dose pedida    : %.0f mL\n",
           dose_ml);
    printf("====================================\n");

    float ultimo_volume =
        volume_inicial;

    int sem_mudanca = 0;

    while(true)
    {
        float volume =
            ler_volume_filtrado();

        float retirado_sensor =
            volume_inicial - volume;

        float retirado =
            retirado_sensor * fator;

        float restante =
            dose_ml - retirado;

        char linha1[17];
        char linha2[17];

        snprintf(linha1,
                 sizeof(linha1),
                 "Dose %.0fmL",
                 dose_ml);

        snprintf(linha2,
                 sizeof(linha2),
                 "Falta %.0f",
                 restante > 0 ? restante : 0);

        lcd_clear();

        lcd_set_cursor(0,0);
        lcd_print(linha1);

        lcd_set_cursor(0,1);
        lcd_print(linha2);

        if(restante <= 0)
            break;

        uint32_t pulso;

        if(restante > 180)
            pulso = PULSO_LONGO_MS;
        else if(restante > 50)
            pulso = PULSO_MEDIO_MS;
        else
            pulso = PULSO_CURTO_MS;

        aplicar_pulso(pulso);

        sleep_ms(TEMPO_ESTABILIZAR_MS);

        uint16_t adc =
            adc_read_raw();

        volume =
            ler_volume_filtrado();

        retirado_sensor =
            volume_inicial - volume;

        retirado =
            retirado_sensor * fator;

        restante =
            dose_ml - retirado;

        printf("T=%.2fV  Vol=%.0fmL  Falta=%.0fmL\n",
               adc_para_tensao(adc),
               volume,
               restante);

        if(fabs(volume - ultimo_volume) < 3.0f)
            sem_mudanca++;
        else
            sem_mudanca = 0;

        ultimo_volume = volume;

        if(sem_mudanca >= MAX_SEM_MUDANCA)
        {
            lcd_clear();

            lcd_set_cursor(0,0);
            lcd_print("ERRO SENSOR");

            lcd_set_cursor(0,1);
            lcd_print("Sem resposta");

            bomba_desligar();

            printf("ERRO SENSOR\n");

            return;
        }
    }

    sleep_ms(1500);

    uint16_t adc_final =
        adc_read_raw();

    float volume_final =
        ler_volume_filtrado();

    printf("\n====================================\n");
    printf("DOSAGEM FINALIZADA\n");
    printf("====================================\n");
    printf("Tensao final  : %.2f V\n",
           adc_para_tensao(adc_final));
    printf("Volume final  : %.0f mL\n",
           volume_final);
    printf("====================================\n");

    lcd_clear();

    lcd_set_cursor(0,0);
    lcd_print("Dose concluida");

    char resultado[17];

    snprintf(resultado,
             sizeof(resultado),
             "%.0fmL OK",
             dose_ml);

    lcd_set_cursor(0,1);
    lcd_print(resultado);

    sleep_ms(3000);
}

int main()
{
    stdio_init_all();

    adc_setup();
    bomba_setup();
    lcd_init_display();

    while(!stdio_usb_connected())
    {
        sleep_ms(100);
    }

    sleep_ms(1000);

    printf("\n");
    printf("====================================\n");
    printf(" SISTEMA DE DOSAGEM AUTOMATICA\n");
    printf("====================================\n");

    while(true)
    {
        mostrar_tela_principal();

        uint16_t adc =
            adc_read_raw();

        float volume =
            ler_volume_filtrado();

        float tensao =
            adc_para_tensao(adc);

        printf("\n");
        printf("====================================\n");
        printf("MENU PRINCIPAL\n");
        printf("====================================\n");
        printf("Volume : %.0f mL\n", volume);
        printf("Tensao : %.2f V\n", tensao);
        printf("====================================\n");
        printf("1 - Calibracao\n");
        printf("2 - Dosar 250 mL\n");
        printf("3 - Dosar 300 mL\n");
        printf("4 - Dosar 350 mL\n");
        printf("Escolha: ");

        char opcao;

        scanf(" %c", &opcao);

        switch(opcao)
        {
            case '1':
                modo_calibracao();
                break;

            case '2':
                dosar(250);
                break;

            case '3':
                dosar(300);
                break;

            case '4':
                dosar(350);
                break;

            default:
                printf("Opcao invalida\n");
                break;
        }
    }

    return 0;
}

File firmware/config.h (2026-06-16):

#ifndef CONFIG_H
#define CONFIG_H

#define ADC_PIN                 26
#define ADC_CHANNEL             0

#define NUM_AMOSTRAS            500

#define BOMBA_PIN               15

#define PULSO_LONGO_MS          1200
#define PULSO_MEDIO_MS           700
#define PULSO_CURTO_MS           300

#define TEMPO_ESTABILIZAR_MS    300

#define FILTRO_LEITURAS          20

#define MAX_SEM_MUDANCA         40

#endif

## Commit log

2026-05-11 Primeiro teste com o potenciometro deslizante
    Raspberry Pi Pico
    ## Funcionalidades atuais
    - Leitura ADC
    - Conversão para porcentagem
    - Filtro por média
    - Histerese
    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
2026-05-12 Revisão das configs e adiçao das bombas e tanques
    Updated ADC calibration values and added tank dimensions and pump pin configurations.
2026-05-12 altura para volume e conversões
2026-05-12 Logica ADC e calculo das misturas
    Refactored ADC reading and added calculations for height and volume based on ADC input. Introduced a mixing calculation for two components with defined percentages.
2026-05-28 Nova versão
    [Mont1.SLDASM, boia.SLDPRT, suporte potenciometro v3.SLDPRT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]
2026-06-01 Refactor main function for ADC reading
    Removed the original main function and replaced it with a simplified version that initializes the system and reads ADC values continuously.
    [main.c]
2026-06-02 Refactor ADC functions and add header file
2026-06-02 Implement ADC setup and reading functions
2026-06-02 Controle de dosagem e interface
    Added user interface for dosage control and feedback.
2026-06-02 Integrate pump control and update dosing logic
    Added functions to control a pump and modified the dosing logic to account for available volume and compensation.
2026-06-02 Update ADC parameters and add approximation settings
2026-06-02 Add function prototypes to adc.h with proper signatures
2026-06-02 Refactor ADC functions for consistency and clarity
2026-06-05 primeiro teste de calibracao
2026-06-05 Refactor CMakeLists.txt for Raspberry Pi Pico project
2026-06-05 Refactor height_to_volume to use calibration factor
    Updated height_to_volume function to include calibration factor.
2026-06-06 Create PCB
2026-06-06 Versão 1 - PCB
2026-06-15 PCB Versão 2
2026-06-16 Revise configuration settings in config.h
    Updated configuration parameters for ADC and pulse timing.
2026-06-16 Add header file for ADC to volume conversion
2026-06-16 Clean up adc.h by removing unnecessary functions
    Removed unused functions related to height and volume calculations.
2026-06-16 Add calibration functions and data for ADC
2026-06-16 Add I2C LCD display functionality
    Implement I2C LCD display functions including initialization, command, data sending, and specific display messages.
2026-06-16 Add files via upload
    Novo suporte de potenciometro, buchas de 8 e 10mm
    [base.SLDPRT, bucha 10.SLDPRT, bucha 8.SLDPRT]
2026-06-17 Add files via upload
    PCB - Versão 3
2026-06-20 Add project description for automated water dosing system
    This README provides a comprehensive overview of an automated water dosing system using Raspberry Pi Pico, detailing its objectives, components, operation, and calibration methods.
2026-06-20 Delete solidworks/suporte potenciometro v3.SLDPRT
    versão antiga
    [suporte potenciometro v3.SLDPRT]
2026-06-20 Delete solidworks/tampa.SLDPRT
    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
    [tampa.SLDPRT]
2026-06-20 Delete solidworks/suporte potenciometro.SLDPRT
    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
    [suporte potenciometro.SLDPRT]
2026-06-20 Delete solidworks/Mont1.SLDASM
    Versão antiga
    [Mont1.SLDASM]
2026-06-21 Versão 4 - PCB
2026-06-22 garantia de todos compilaveis
2026-06-22 Revise README com informações do projeto e resultados
    Atualiza a seção de integrantes, descrição e objetivos do projeto, além de adicionar detalhes sobre a estratégia de controle e resultados obtidos.
2026-06-26 Restore CMakeLists.txt for Raspberry Pi Pico setup
2026-06-28 CAD Suporte eletrônica
    [Montagem.SLDASM, chão.SLDPRT, frente.SLDPRT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]
